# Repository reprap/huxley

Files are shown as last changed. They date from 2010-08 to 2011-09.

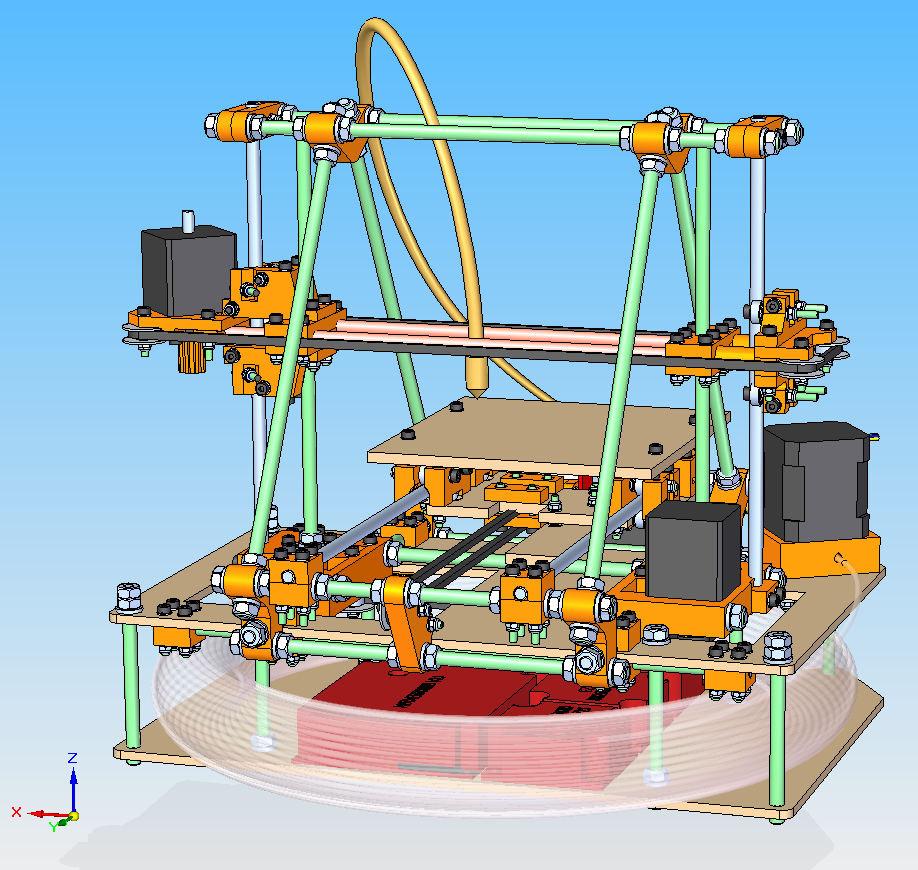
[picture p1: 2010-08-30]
Documentation/perspective-front-transparent-reel.PNG

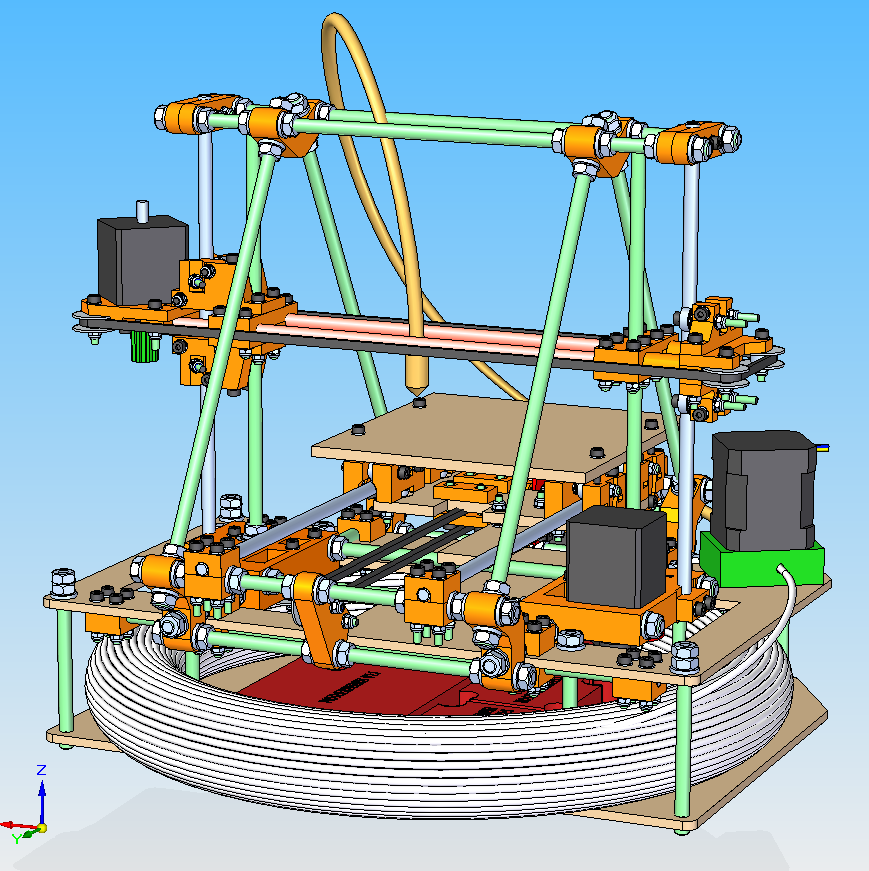
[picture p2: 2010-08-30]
Documentation/perspective-front.PNG

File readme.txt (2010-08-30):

The Mini-Mendel design is based on M3 Nuts and Bolts, M6 threaded rod, rather than M4s and M8s, giving a much more compact design. The build area is approximately equal to 100 x 100 mm; critically the replication time has been reduced by 66% N.B.  This is experimental and not supported.  The filament feed is also known not to work, and a bowden extruder is required.

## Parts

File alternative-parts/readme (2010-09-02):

The x extenders are based on Whosawhatsis's Thingiverse objects at http://www.thingiverse.com/thing:3616

The sandwich spacer is needed because I removed the under-dents from the X motor mount.

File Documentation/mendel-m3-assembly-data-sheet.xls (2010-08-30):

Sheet: Costing
Cost type | UK RS £ | Notes
Bar | £8.55
Bearings | £49.00
Belt | £15.01
Extruder parts | £15.00 | Guess
Fasteners | £70.50
Motors | £80.00 | Approx
PCB/Electronics | £110.00
Thin sheet | £0.00
RP | £20.00 | Assume no comission
Thick sheet | £20.00 | Guess
Studding | £6.56
Total | 394.62
M4
Cost type | UK estimate | Notes
Bar | £11.19 | RS
Bearings | £31.20 | RS
Belt | £23.33 | RS
Extruder parts | £15.00 | Estimate
Fasteners | £74.21 | RS
Motors | £80.00 | Assumes 4x NEMA 17s
PCB/Electronics | £110.00 | Zach's Gen3 electronics
Thin sheet | £0.00 | Beer can
RP | £20.00 | Assumes no commission
Thick sheet | £20.00 | Estimate
Studding | £11.65 | RS
Total | £396.58

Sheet: M3 BOM (Temp)
Part | Qty | Type | Net RP volumes (mm^3) | UK RS number | UK RS cost | Note
bed2.par | 1 | Thick sheet | 0
pcb-carriage-board.par | 1 | Thick sheet | 0
purge-plate.par | 1 | Thick sheet | 0
stud-bedstad.par | 4 | Studding | 0 | 530321 | 6.59
stud-frame-end-top.par | 2 | Studding | 0
stud-frame-end.par | 4 | Studding | 0
stud-frame-side.par | 6 | Studding | 0
stud-z-base-long.par | 1 | Studding | 0
stud-z-base-short.par | 1 | Studding | 0
stud-z-leadscrew.par | 2 | Studding | 0
x-bar.par | 2 | Bar | 0 | 682062 | 8.55
x-belt.par | 1 | Belt | 0 | 4745779 | 8.28
y-bar.par | 2 | Bar | 0
y-belt.par | 1 | Belt | 0 | 4745606 | 6.73
y-chassis2.par | 1 | Thick sheet | 0
y-flag.par | 1 | Thin sheet | 0
z-bar.par | 2 | Bar | 0
z-belt.par | 1 | Belt | 0
bar-distance_0off.par | 1 | RP | 0
drive-pulley_3off.par | 3 | RP | 6093.222
foot.par | 4 | RP | 0
frame-vertex_6off.par | 6 | RP | 53465.424
x-180-bearing-clamp.par | 2 | RP | 8938.892
x-axis-clamp_4off.par | 4 | RP | 23020.188
x-axis-sandwich-clamp.par | 1 | RP | 3505.997
x-axis-spacer_2off.par | 2 | RP | 2010.62
x-bar-clamp_1off.par | 1 | RP | 2968.35
x-bearing-clamp_2off.par | 2 | RP | 25948.946
x-blunt-plate.par | 1 | RP | 5375.906
x-motor-end-clamp_1off.par | 1 | RP | 11635.749
y-bar-clamp_4off.par | 8 | RP | 18386.904
y-bearing-180.par | 4 | RP | 18829.152
y-bearing-360-bracket1.par | 4 | RP | 16690.904
y-belt-clamp.par | 2 | RP | 3178.416
y-belt-nut-trap.par | 2 | RP | 3585.404
y-idler-bracket.par | 1 | RP | 7615.935
y-motor-bracket.par | 1 | RP | 15330.214
z-bar-bottom-clamp.par | 2 | RP | 2946.722
z-bar-top-clamp.par | 4 | RP | 16145.84
z-driven-pulley-rim.par | 4 | RP | 4048.132
z-driven-pulley.par | 2 | RP | 4202.194
z-leadscrew-base-motor.par | 1 | RP | 41331.698
z-leadscrew-base-tensioner.par | 1 | RP | 38976.95
extruder-controller-v2-2.par | 1 | Electronics | 0
opto-endstop-v2-1-pcb.par | 1 | Electronics | 0
optoswitch-rs304560.par | 1 | Electronics | 0
reprap-mother-board-v1.1.par | 1 | Electronics | 0
stepper-motor-driver-v2-3.par | 3 | Electronics | 0
623-bearing.par | 33 | Bearing | 0 | 6189884 | 39.5
m3-capx12.par | 19 | Fastener | 0 | 4915209 | 10.69
m3-capx20.par | 43 | Fastener | 0 | 483819 | 11.05
m3-capx30.par | 74 | Fastener | 0 | 4679846 | 22.32
m3-nut.par | 33 | Fastener | 0 | 560293 | 4.09
m3-nylock.par | 108 | Fastener | 0 | 524281 | 7.1
m3-washer.par | 346 | Fastener | 0 | 560338 | 2.72
m5-mudguard-washer.par | 15 | Fastener | 0 | 6667753 | 2.99
626-bearing.par | 10 | Bearing | 0 | 6190014 | 9.5
m6-nut.par | 112 | Fastener | 0 | 525919 | 6.99
m6-washer.par | 132 | Fastener | 0 | 525947 | 2.55
stepper-motor-nema14-fl35ST36-1004a-motioncontrol.par | 2 | Motor | 0
stepper-motor-nema14-fl35st36-1004b-motioncontrol.par | 1 | Motor | 0
pinch-wheel-bracket-603-nema17-bowden.par | 1 | RP | 31637.835
 |  | Total volume (cm^3) | 365.869594
 |  | M4 volume (cm^3) | 1114
 |  | M3 % of M4 | 32.84287199%
 |  |  | OMG

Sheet: Mendel M3 lengths
BAR & JIG LENGTHS (READ NOTES TAB) |  |  |  |  |  |  |  | BELT SPECIFICATIONS (READ NOTES TAB)
Bar | Name | ø (mm) | Type | Length (mm) | Qty | From 1m stud # | From .33m bar # | Belt | Name | Type | Pitch (mm) | Width (mm) | Length range | Length* (mm) | Qty | US | UK | NZ
A | Stud-frame-end-top | M6 | Studding | 270 | 2 | 4 |  | BX | x-belt | Ended | 5 | 4 | Min | 785 | 1 |  | RS 4745779 (http://uk.rs-online.com/web/search/searchBrowseAction.html?method=getProduct&R=4745779)
B | Stud-frame-side | M6 | Studding | 244 | 6 | 1,2 |  | BY | y-belt | Ended | 5 | 4 | Min |  | 1 | split BX
C | Stud-frame-end | M6 | Studding | 183 | 4 | 3 |  | BZ | z-belt | Continuous | 5 | 4 | From | 520-560 | 1 |  | RS 4745606 (http://uk.rs-online.com/web/search/searchBrowseAction.html?method=getProduct&R=4745606)
D1 | Stud-z-base-beam-short | M6 | Studding | 230 | 1 | 2
D2 | Stud-z-base-beam-long | M6 | Studding | 257 | 1 | 2
E | Stud-z-leadscrew | M6 | Studding | 230 | 2 | 3,4
X | x-bar | 6 | Bar | 275 | 2 |  | 1,2
Y | y-bar | 6 | Bar | 272 | 2 |  | 3,4
Z | z-bar | 6 | Bar | 224 | 2 |  | 5,6
J1 |  | ~6 | Scrap/stud | 200 | 1 | 5
J2 |  | ~6 | Scrap/stud | 140 | 1 | 5
J3 |  | ~6 | Scrap/stud | 99 | 1 | 5
 | Stud-base-top-horizontal | M6 | Studding | 320 | 2
 | Stud-reel-enclosure-pin | M6 | Studding | 84 | 4
 | Stud-bed-pillar | M6 | Studding | 82 | 4
 | Stud filament | M6 | Studding | 102 | 4
Total number of 1m lengths needed of studding =
Total number of .33m lengths needed of bar =
INSPECTION DISTANCES FOR SQUARING (PERFECT MODEL) (READ NOTES TAB)
Label | Measurement (mm)
M1 | 240
M2 | 29
M3 | 42
M4 | 60
M5 | 128 | Between two leadscrew bases (from inner face to inner face)
M6 | 170 | Between inner faces of x-axis ends

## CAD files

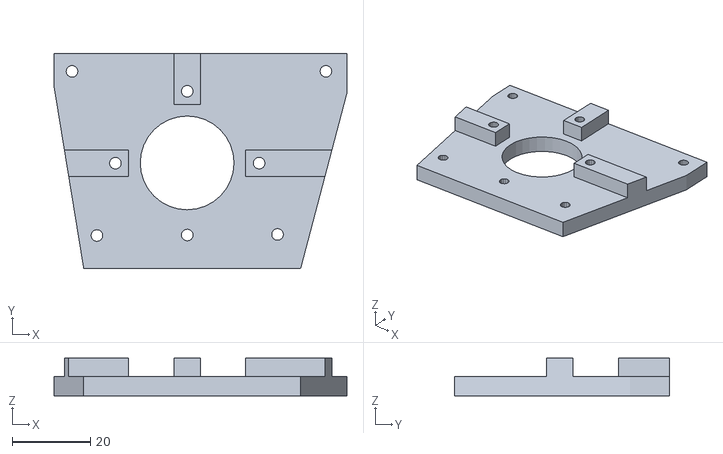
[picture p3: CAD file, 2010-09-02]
alternative-parts/x-motor-end-clamp-extended.stl
75.0 x 55.0 x 9.70

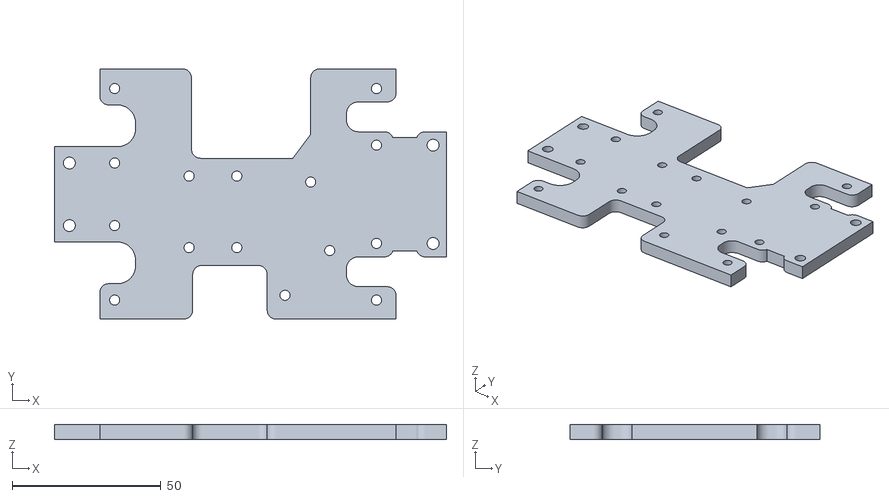
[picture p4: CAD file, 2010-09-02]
Cut-sheet-parts/y-chassis2_2.stl
131.6 x 84.0 x 5.00

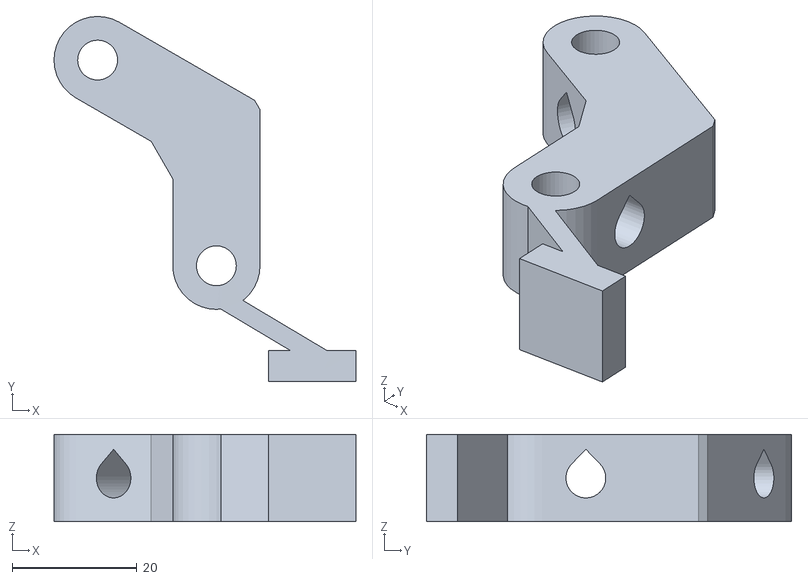
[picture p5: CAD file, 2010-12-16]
frame-vertex-with-foot-4off.stl
48.5 x 58.6 x 14.0

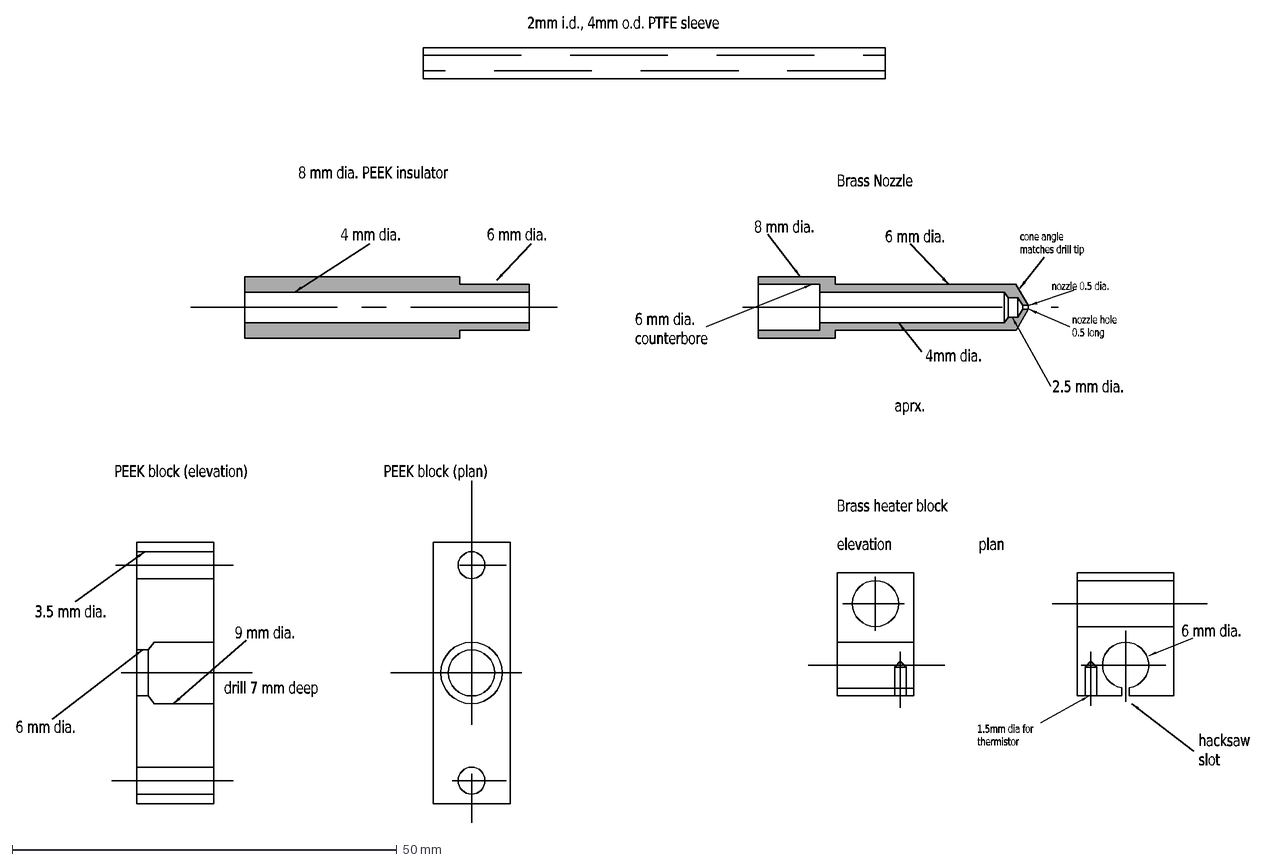
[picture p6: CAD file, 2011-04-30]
OpenSCAD-huxley/Design-drawings/hot-end.dxf
PEEK\~block\~(elevation)
PEEK\~block\~(plan)
drill\~7\~mm\~deep
hacksaw slot
1.5mm\~dia\~for thermistor
nozzle\~0.5\~dia.
cone\~angle matches\~drill\~tip
Brass\~Nozzle
Brass\~heater\~block elevation\~\~\~\~\~\~\~\~\~\~\~\~\~\~\~\~\~\~\~\~\~\~\~plan
nozzle\~hole\~ 0.5\~long
6\~mm\~dia. counterbore
8\~mm\~dia.
6\~mm\~dia.
2.5\~mm\~dia.
8\~mm\~dia.\~PEEK\~insulator
3.5\~mm\~dia.
9\~mm\~dia.
4\~mm\~dia.
aprx.
4mm\~dia.
2mm\~i.d.,\~4mm\~o.d.\~PTFE\~sleeve

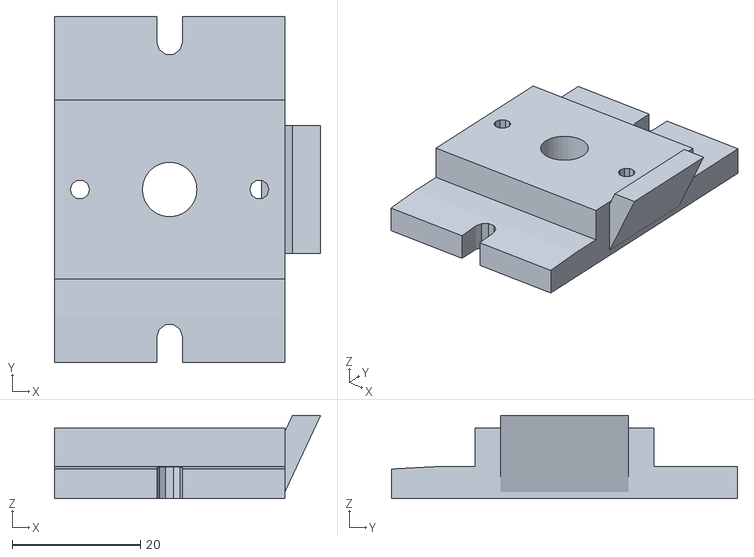
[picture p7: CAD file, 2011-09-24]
OpenSCAD-huxley/STLs/extruder-mendel-base-plate.stl
41.6 x 54.0 x 13.0

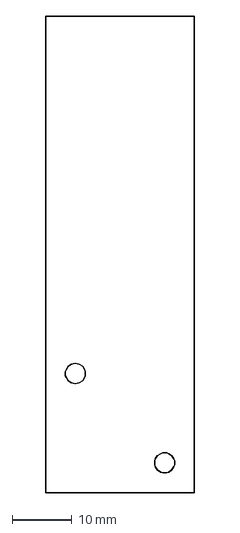
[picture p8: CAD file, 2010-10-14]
Original-CAD/custom-imported-parts/purge-plate.dxf
25.0 x 80.0 mm

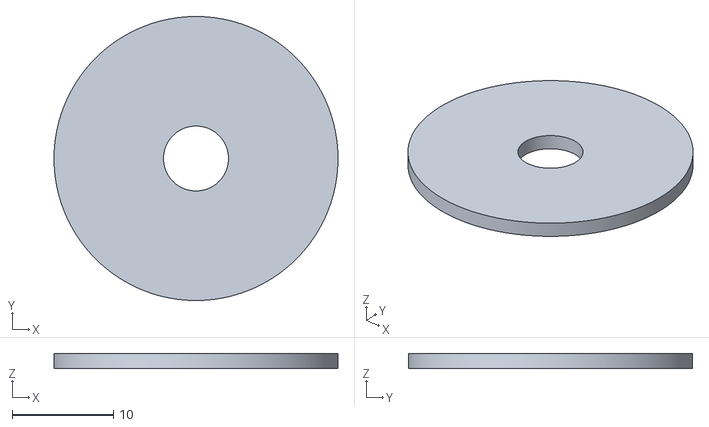
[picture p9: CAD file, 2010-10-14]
Original-CAD/printed-parts/z-driven-pulley-rim.stl
28.0 x 28.0 x 1.50

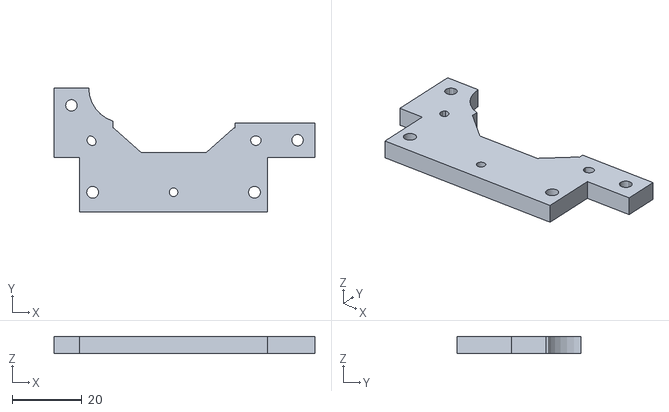
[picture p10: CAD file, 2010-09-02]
alternative-parts/x-blunt-plate-extended.stl
75.0 x 35.6 x 5.00

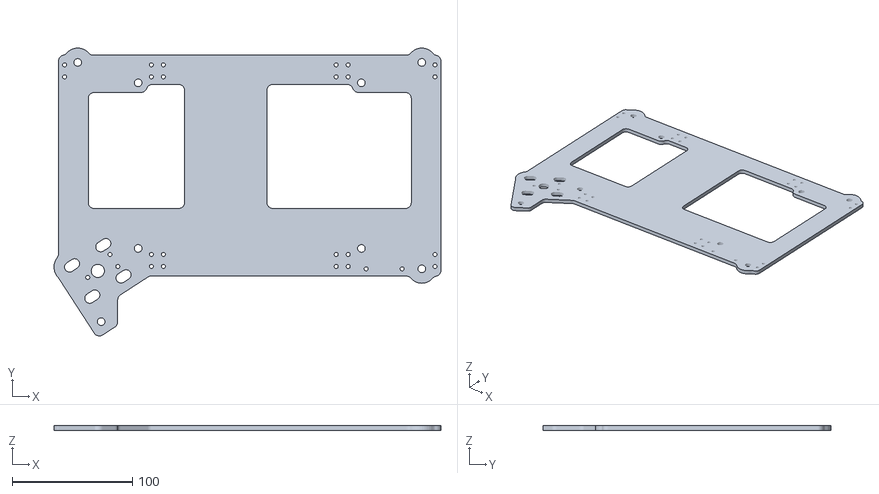
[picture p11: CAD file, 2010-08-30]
Cut-sheet-parts/base-sheet-top.stl
322.5 x 239.9 x 4.00

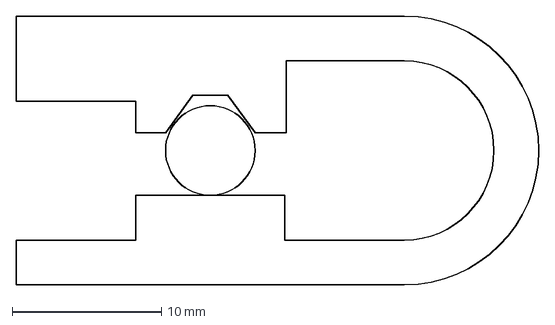
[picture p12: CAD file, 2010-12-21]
OpenSCAD-huxley/Design-drawings/bearing360.dxf
35.0 x 18.0 mm

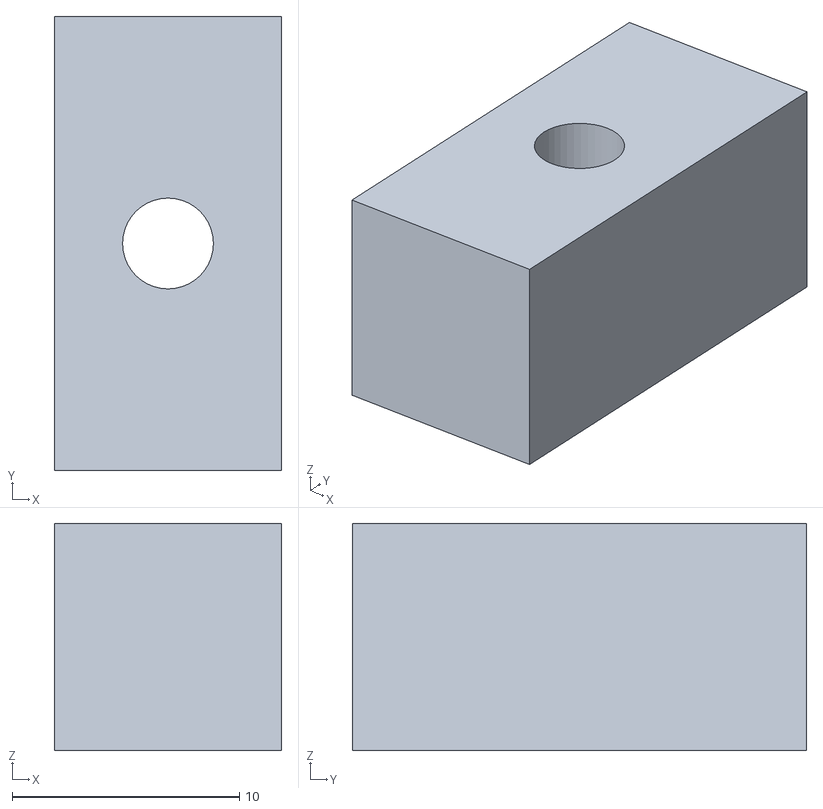
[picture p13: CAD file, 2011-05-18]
OpenSCAD-huxley/STLs/extruder-prusa-spacer.stl
10.0 x 20.0 x 10.0

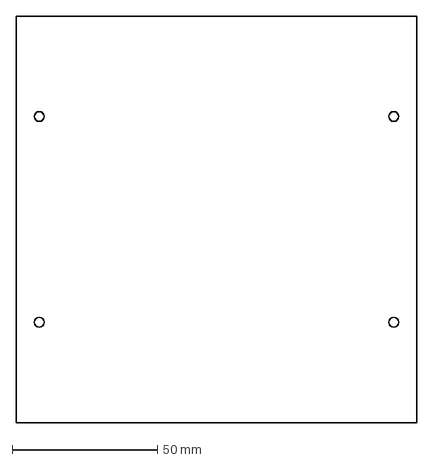
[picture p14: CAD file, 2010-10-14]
Original-CAD/custom-imported-parts/bed.dxf
138.1 x 140.0 mm

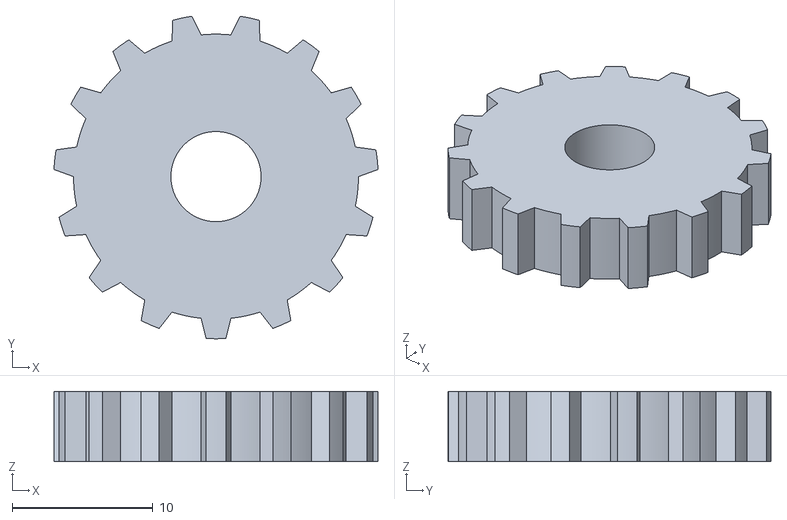
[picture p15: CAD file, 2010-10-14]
Original-CAD/printed-parts/z-driven-pulley.stl
23.0 x 22.9 x 5.00

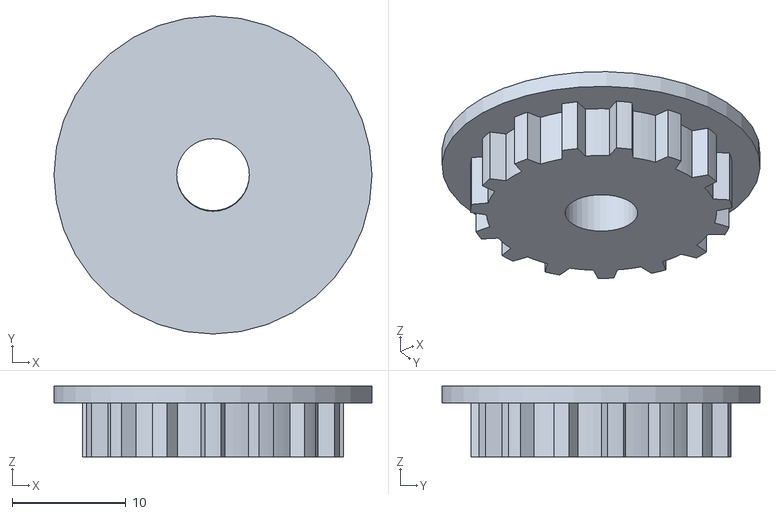
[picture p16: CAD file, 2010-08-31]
z-driven-pulley-2off.stl
28.0 x 28.0 x 6.25

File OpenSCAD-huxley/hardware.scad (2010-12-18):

include <settings.scad>;


module rod(length, threaded) if (threaded && renderrodthreads) {
	linear_extrude(height = length, center = true, convexity = 10, twist = -360 * length / rodpitch, $fn = fn)
		translate([rodsize * 0.1 / 2, 0, 0])
			circle(r = rodsize * 0.9 / 2, $fn = fn);
} else cylinder(h = length, r = rodsize / 2, center = true, $fn = fn);


module rodnut(position, washer) render() translate([0, 0, position]) {
	intersection() {
		scale([1, 1, 0.5]) sphere(r = 1.05 * rodsize, center = true);
		difference() {
			cylinder (h = rodnutsize, r = rodnutdiameter / 2, center = true, $fn = 6);
			rod(rodnutsize + 0.1);
		}
	}
	if (washer == 1 || washer == 4) rodwasher(((position > 0) ? -1 : 1) * (rodnutsize + rodwashersize) / 2);
	if (washer == 2 || washer == 4) rodwasher(((position > 0) ? 1 : -1) * (rodnutsize + rodwashersize) / 2);
}


module rodwasher(position) render() translate ([0, 0, position]) difference() {
	cylinder(r = rodwasherdiameter / 2, h = rodwashersize, center = true, $fn = fn);
	rod(rodwashersize + 0.1);
}


module screw(length, nutpos, washer, bearingpos = -1) union(){
	translate([0, 0, -length / 2]) if (renderscrewthreads) {
		linear_extrude(height = length, center = true, convexity = 10, twist = -360 * length / screwpitch, $fn = fn)
			translate([screwsize * 0.1 / 2, 0, 0])
				circle(r = screwsize * 0.9 / 2, $fn = fn);
	} else cylinder(h = length, r = screwsize / 2, center = true, $fn = fn);
	render() difference() {
		translate([0, 0, screwsize / 2]) cylinder(h = screwsize, r = screwsize, center = true, $fn = fn);
		translate([0, 0, screwsize]) cylinder(h = screwsize, r = screwsize / 2, center = true, $fn = 6);
	}
	if (washer > 0 && nutpos > 0) {
		washer(nutpos);
		nut(nutpos + washersize);
	} else if (nutpos > 0) nut(nutpos);
	if (bearingpos >= 0) bearing(bearingpos);
}


module bearing(position) render() translate([0, 0, -position - bearingwidth / 2]) union() {
	difference() {
		cylinder(h = bearingwidth, r = bearingsize / 2, center = true, $fn = fn);
		cylinder(h = bearingwidth * 2, r = bearingsize / 2 - 1, center = true, $fn = fn);
	}
	difference() {
		cylinder(h = bearingwidth - 0.5, r = bearingsize / 2 - 0.5, center = true, $fn = fn);
		cylinder(h = bearingwidth * 2, r = screwsize / 2 + 0.5, center = true, $fn = fn);
	}
	difference() {
		cylinder(h = bearingwidth, r = screwsize / 2 + 1, center = true, $fn = fn);
		cylinder(h = bearingwidth + 0.1, r = screwsize / 2, center = true, $fn = fn);
	}
}


module nut(position, washer) render() translate([0, 0, -position - nutsize / 2]) {
	intersection() {
		scale([1, 1, 0.5]) sphere(r = 1.05 * screwsize, center = true);
		difference() {
			cylinder (h = nutsize, r = nutdiameter / 2, center = true, $fn = 6);
			cylinder(r = screwsize / 2, h = nutsize + 0.1, center = true, $fn = fn);
		}
	}
	if (washer > 0) washer(0);
}


module washer(position) render() translate ([0, 0, -position - washersize / 2]) difference() {
	cylinder(r = washerdiameter / 2, h = washersize, center = true, $fn = fn);
	cylinder(r = screwsize / 2, h = washersize + 0.1, center = true, $fn = fn);
}


rod(20);
translate([rodsize * 2.5, 0, 0]) rod(20, true);
translate([rodsize * 5, 0, 0]) screw(10, true);
translate([rodsize * 7.5, 0, 0]) bearing();
translate([rodsize * 10, 0, 0]) rodnut();
translate([rodsize * 12.5, 0, 0]) rodwasher();
translate([rodsize * 15, 0, 0]) nut();
translate([rodsize * 17.5, 0, 0]) washer();

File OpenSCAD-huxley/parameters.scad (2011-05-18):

// Parameters file for RepRap Huxley (and maybe Mendel)

// Set ONE OF these true.

huxley=false;
mendel=!huxley;



pi=3.14159265;

// The relative location in your file system where the .dxf files are
// DXFs are for quick development.  They should be replaced by parameterised CSG in due course.

fileroot="Design-drawings/";

rodsize = 6;	//threaded/smooth rod diameter in mm
xaxis = 182.5;	//width of base in mm
yaxis = 266.5;	//length of base in mm


screwsize = 3;	//bearing bore/screw diameter in mm
bearingsize = 10;	//outer diameter of bearings in mm
bearingwidth = 4;	//width of bearings in mm


rodpitch = rodsize / 6;
rodnutsize = 0.8 * rodsize;
rodnutdiameter = 1.9 * rodsize;
rodwashersize = 0.2 * rodsize;
rodwasherdiameter = 2 * rodsize;
screwpitch = screwsize / 6;
nutsize = 0.8 * screwsize;
nutdiameter = 1.9 * screwsize;
pentanutradius=1.04*screwsize;
washersize = 0.2 * screwsize;
washerdiameter = 2 * screwsize;
partthick = 2 * rodsize;
vertexrodspace = 2 * rodsize;


c = [0.3, 0.3, 0.3];
rodendoffset = rodnutsize + rodwashersize * 2 + partthick / 2;
vertexoffset = vertexrodspace + rodendoffset;


renderrodthreads = false;
renderscrewthreads = false;
fn = 36;

// The gap between the joining rods at a vertex

vertex_radius=sqrt(rodsize*rodsize + vertexoffset*vertexoffset);
vertex_ang = atan(vertexoffset/rodsize)-30;
vertex_gap = 2*vertex_radius*cos(vertex_ang);

// Nema 17 dimensions - these are absolute

nema17_square=42;
nema17_screws=31;
nema17_screw_r=1.5;
nema17_hub=22;
nema17_hub_depth=2;
nema17_length=36;
nema17_shaft=5;
nema17_shaft_length=55;
nema17_shaft_projection=22;

// Nema 14 dimensions - these are absolute

nema14_square=35.3;
nema14_screws=26;
nema14_screw_r=1.5;
nema14_hub=22;
nema14_hub_depth=2;
nema14_length=36;
nema14_shaft=5;
nema14_shaft_length=66;
nema14_shaft_projection=19;

// Nema 11 dimensions - these are absolute

nema11_square=28.5;
nema11_screws=23;
nema11_screw_r=1.25;
nema11_hub=22;
nema11_hub_depth=2;
nema11_length=44.5;
nema11_shaft=5;
nema11_shaft_length=78;
nema11_shaft_projection=18;

// Limit switch parameters

limit_switch_hole_diameter=2.5;
limit_switch_centres=9.5;

// The RepRap slide bearings

bearing_mount_centres=18;
bearing_width=7;
bearing_depth=18;

// X axis parameters - many should be relative

x_bar_gap=30;
motor_center_y = 26;
bar_clamp_x=5;
bar_clamp_y=8;
bar_clamp_x_gap=23;
bearing_y=50;
bearing_x=bar_clamp_x_gap + 10;
hole_land=4;
thickness=5;
bearing_low_z = 8;
bearing_z_gap = 25;
bearing_plate_width = bearing_mount_centres+2*hole_land + 10;
bearing_plate_overlap=0.5;
bearing_plate_support=10;

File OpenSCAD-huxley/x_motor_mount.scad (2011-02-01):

// X motor mount

// Adrian Bowyer 18 December 2010

include <parameters.scad>;
use<library.scad>

screw_hole_r=screwsize/2;

//*****************************************************************************************************************

module base()
{
	x_size = 2*hole_land + 2*bearing_x;
	y_size = bearing_y + hole_land;
	difference()
	{
		difference()
		{
			translate([-bearing_x - hole_land, 0, -thickness])
				cube([x_size, y_size, 2*thickness]);
			translate([-bar_clamp_x_gap - hole_land, 0, -bearing_x])
				rotate(a = 105, v = [0, 0, 1])
					cube([2*bearing_y ,2*bearing_y , 8*thickness]);
			translate([bar_clamp_x_gap+ hole_land, 0, -4*thickness])
				rotate(a = -15, v = [0, 0, 1])
					cube([2*bearing_y ,2*bearing_y , 8*thickness]);
		}
		difference()
		{
			translate([-x_size-1, -1, 0])
				cube([2+ 2*x_size, y_size+2, 6*thickness]);
			translate([0, motor_center_y, 0])
				rotate(a = 45, v = [0, 0, 1])
					translate([ - nema14_square*0.5,  - nema14_square*0.5, 0])
						cube([nema14_square, nema14_square, 2*thickness]);
		}
	}
}

module oriented_teardrop()
{
	translate([0, -2.5*thickness, 0])
		rotate(a = 90, v = [0, 0, 1])
			rotate(a = 90, v = [0, 1, 0])
				teardrop(r=screw_hole_r, h=4*thickness, truncateMM=-1);
}

module bearing_plate()
{

		difference()
		{
			union()
			{
			translate([-bearing_plate_width/2, bearing_plate_overlap - thickness, -thickness])
			{
				difference()
				{
					cube([bearing_plate_width, thickness + bearing_plate_support, 
						bearing_low_z + bearing_z_gap + hole_land + thickness]);
					translate([thickness, thickness, - 5])
						cube([bearing_plate_width - 2*thickness, 2*thickness + bearing_plate_support, 
							bearing_low_z + bearing_z_gap + hole_land + thickness + 10]);
				}
			}
		// Shim support ledges

		translate([-bearing_mount_centres/2, -0.8*thickness, bearing_low_z + bearing_z_gap-1.5*thickness-1.5])
			intersection()
			{
				rotate([35,0,0])
					cube([bearing_mount_centres, thickness, thickness]);
				translate([-thickness/5, -thickness*3/5, -thickness*6/5])
					cube([2*bearing_mount_centres, 2*thickness, 2*thickness]);
			}

		translate([-bearing_mount_centres/2, -0.8*thickness, bearing_low_z -1.5*thickness-1.5])
			intersection()
			{
				rotate([35,0,0])
					cube([bearing_mount_centres, thickness, thickness]);
				translate([-thickness/5, -thickness*3/5, -thickness*6/5])
					cube([2*bearing_mount_centres, 2*thickness, 2*thickness]);
			}
			}

			// Bearing mount holes
	
			for ( y = [0:1] )
			for ( x = [0:1] ) 
			{
				translate([(x-0.5)*bearing_mount_centres, 0, bearing_low_z + y*bearing_z_gap])
					oriented_teardrop();
			}
	
			// Limit switch mounting holes
	
			translate([-40,1,15])
				rotate([0,90,0])
				{
					teardrop(r=limit_switch_hole_diameter/2, h=40, truncateMM=-1);
					translate([0,0,27])
						teardrop(r=limit_switch_hole_diameter, h=18, truncateMM=-1);
				}
			translate([-40,1,15+limit_switch_centres])
				rotate([0,90,0])
				{
					teardrop(r=limit_switch_hole_diameter/2, h=40, truncateMM=-1);
					translate([0,0,27])
						teardrop(r=limit_switch_hole_diameter, h=18, truncateMM=-1);
				}
			}



}

module cylindrical_z_holes()
{
	union()
	{
		translate([-bar_clamp_x_gap, bar_clamp_y, 0])
			cylinder(r = screw_hole_r, h = 30, center = true, $fn=10);
		translate([bar_clamp_x_gap, bar_clamp_y, 0])
			cylinder(r = screw_hole_r, h = 30, center = true, $fn=10);
		translate([-bearing_x, bearing_y, 0])
			cylinder(r = screw_hole_r, h = 30, center = true, $fn=10);
		translate([bearing_x, bearing_y, 0])
			cylinder(r = screw_hole_r, h = 30, center = true, $fn=10);
		translate([0, motor_center_y, thickness])
			rotate(a = 45, v = [0, 0, 1])
				nema14(body=false, counterbore = -1);
	}
}

module x_motor_mount()
{
	union()
	{
		bearing_plate();
		difference()
		{
			base();
			cylindrical_z_holes();
		}
	}
}


x_motor_mount();

/*translate([0, motor_center_y, thickness])
	rotate(a = 45, v = [0, 0, 1])
		nema14(body=true, counterbore = -1);*/

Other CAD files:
alternative-parts/y-bar_clamp_M6-4-off.stl
Cut-sheet-parts/purge-plate_2.stl
drive-pulley_3off.stl
OpenSCAD-huxley/Design-drawings/bearing180.dxf
OpenSCAD-huxley/y_axis_motor_mount_and_limit_switch_holder.scad
Cut-sheet-parts/base-sheet-bottom.stl
Cut-sheet-parts/bed2.stl
OpenSCAD-huxley/Extruders/universal-1.75mm-filament-extruder.scad
OpenSCAD-huxley/Old-Extruder-Designs/original-extruder.scad
OpenSCAD-huxley/Old-Extruder-Designs/simple-extruder.scad
OpenSCAD-huxley/Original-files/Huxley.scad
OpenSCAD-huxley/Original-files/carriage.scad
OpenSCAD-huxley/Original-files/carriagetry.scad
OpenSCAD-huxley/Original-files/platformheater.scad
OpenSCAD-huxley/Original-files/teardrop.scad
OpenSCAD-huxley/Original-files/x_carriage.scad
OpenSCAD-huxley/Original-files/x_z_interface.scad
OpenSCAD-huxley/Original-files/y_bar_clamp.scad
OpenSCAD-huxley/Original-files/y_bar_clamp_old.scad
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

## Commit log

2010-08-30 Tidying Huxley files.
    [huxley-trays.ods]
2010-08-31 Huxley tidying.
    [z-driven-pulley-rim-2off.stl, z-driven-pulley.stl]
2010-09-02 More work on Huxley design.
    [huxley-trays.ods, x-blunt-plate-extended.stl, x-motor-end-clamp-extended.stl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]
2010-10-13 Created a directory for the original CAD files from Ed.
2010-10-14 Uploading original solid edge files for Huxley
    [Asm1.cfg, YMotor.cfg, base-bottom.cfg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]
2010-10-24 Possible slide bearing design for Huxley added. WIP.
2010-12-16 Feet added to Huxley.
    [frame-vertex-with-foot-4off.stl, frame-vertex_2off.stl]
2010-12-18 Starting to put together work on an OpenSCAD version of Huxley. A lot of this is from
    https://github.com/timschmidt/parameterized-mendel/tree/master/experimental/huxley/
    [bearing.scad, bearing180.dxf, bearing360.dxf]
2010-12-18 More from
    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
    [Huxley.scad, carriage.scad, carriagetry.scad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]
2010-12-18 More OpenScad huxley.
    [x-motor-mount.dxf, x_motor_mount.scad]
2010-12-19 Minor improvements to bearing script.
    [bearing.scad]
2010-12-19 New X motor mount design added.
    [nema14_motor.scad, settings.scad, teardrop.scad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]
2010-12-19 More messing about with the Huxley design.
    [bearing.scad, bearing180.dxf, bearing360.dxf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]
2010-12-21 Creating a Huxley frame vertex with an adjuster to allow the Y axis rods to be the way the bed is levelled.
    [frame_vertex.scad]
2010-12-22 Reorganising the Huxley OpenSCAD files.
    [Huxley.scad, bearing.scad, carriage.scad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]
2010-12-22 More messing about with the OpenSCAD Huxley design.
    [bearing.scad, frame_vertex.scad, library.scad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]
2010-12-23 Fixed accidental deletion of frame vertex...
    [frame_vertex.scad]
2011-03-25 Mods to Huxley extruder to make assembly easier.
    [bom.ods, extruder.scad]
2011-03-31 Even smaller simpler Huxley extruder design. WIP.
    [library.scad, parameters.scad, simple-extruder.scad]
2011-04-04 Simple extruder WIP.
    [simple-extruder.scad]
2011-04-09 Combining Huxley experimental extruder designs into one master design.
    [new-extruder.scad]
2011-04-09 Combining Huxley experimental extruder designs into one master design. WIP.
    [new-extruder.scad]
2011-04-11 New super (?) extruder WIP.
    [new-extruder.scad]
2011-04-13 Organising extruder designs.
    [original-extruder.scad, simple-extruder.scad, universal-1.75mm-filament-extruder.scad]
2011-04-13 Working (?) Huxley Mini-extruder design.
    [universal-1.75mm-filament-extruder.scad]
2011-04-14 Organising mini-extruder files.
    [extruder.sch, hot-end.dxf]
2011-04-18 Huxley extruder design. WIP.
    [parameters.scad, universal-1.75mm-filament-extruder.scad]
2011-04-23 Huxley extruder design.
    [hot-end.dxf]
2011-04-24 Added mini extruder spacer for Prusa X carriage.
    [hot-end.dxf, universal-1.75mm-filament-extruder.scad]
2011-04-25 Huxley extruder design. A few corrections.
    [universal-1.75mm-filament-extruder.scad]
2011-04-26 Changed Huxley limit switch mounts.
    [y_axis_motor_mount_and_limit_switch_holder.scad]
2011-04-29 Huxley design.
    [cylinder_clamp.scad, parameters.scad, x_axis_z_nut_holder_and_x_cable_holder_clamp.scad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]
2011-04-30 Huxley extruder design. Improved hot-end liner.
    [hot-end.dxf]
2011-05-18 Added Universal extruder STLs. Changed Prusa spacer height to use more common screw size.
    [extruder-drive-gear.stl, extruder-driven-gear.stl, extruder-duct-1.stl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]
2011-09-24 Improved desigh of extruder base plate.
    [extruder-mendel-base-plate.stl, universal-1.75mm-filament-extruder.scad]
